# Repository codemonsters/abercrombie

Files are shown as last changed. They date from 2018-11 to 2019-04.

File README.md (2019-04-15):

# Abercrombie

Four-legged educational and minimalist robot using an Arduino Nano board, two SG90 servos and five easy to print parts.

Its design is extremelly simple and it is meant to be used in the classroom or by anyone who wants to build his first robot from scratch.

([versión en español aquí](README.es.md))

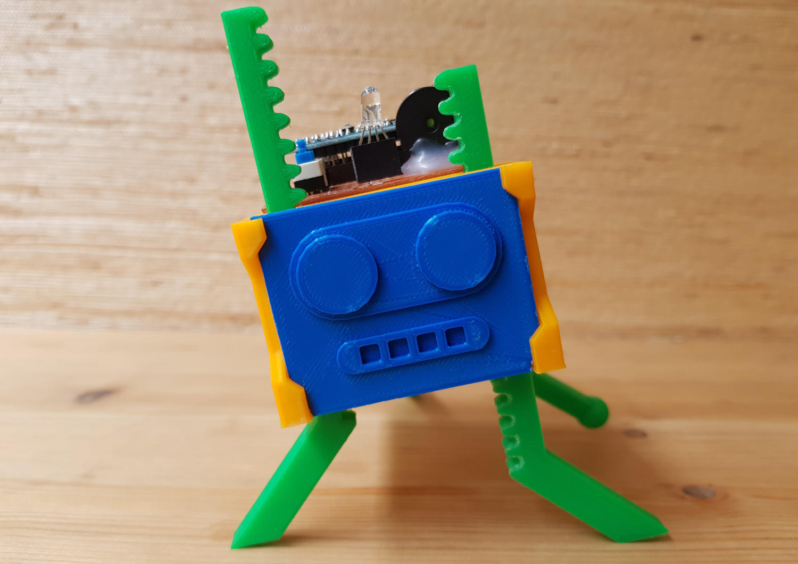
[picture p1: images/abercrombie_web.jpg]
Abercrombie


## Motivation

The general design and also the mechanism that allows the robot to move around is based in an awesome project by Randy Sarafan [published here](https://www.instructables.com/id/3D-Printed-Robot/). After reaching the project for the first time and building one it seemed that a four-legged minimalist robot like his is a great idea. For didactic purposes it would be great to have a similar one but just smaller, easier to print and build with components even cheaper and easier to find in any place you live.

So the robot was designed to be built, customized and programmed in the classroom. It wants to be a starting point so kids, teenagers and of course anyone else interested can created his first walking robot. Its design is intentionally simplistic, trying to be friendly even for people not initiated in programming, electronics or 3D printing.

The robot can be used in educational activities dedicated to different aspects of robotics:

* Work only in the design and 3D printing customizing the robot with our own designs, assembling it with just a scissor and a screwdriver.
* Turn the activity more into electronics making use of perfboards, soldering irons and including different electronic components.
* Use the robot for programming activities: defining the instructions that form every movement or creating programs that control any sensor or actuator we have attached to the robot.
* Treat all the pointed challenges together.

## General characteristics

Pros:

* Simple and completely open design with a very permissive license (GPL3 for the code and CC BY-NC-SA 4.0 for the 3D printed parts).
* Standard and extremelly simple electronics: mostly just two SG90 servos, one Arduino Nano board, a Nano sensor shield (or a perfboard) and a 9V battery.
* Very easy to print: just a few parts of reduced size that don't need support material while printing.
* Customizable: Creating new designs for any of his parts, but also because the chassis has connectors in the front area to attach any new piece designed by us.
* Extensible: After soldering an Arduino Nano board the perfboard should have enough free space to add extra components: a buzzer, LED lights, an ultrasonic sensor, LDR resistors...
* It is a four-legged robot. And a bit clumsy, but it is also friendly looking and funny while walking.

Cons:

* It is a four-legged robot. Sure this is also and disadvantage and his movement is not suited for certain activities where robots with wheels are much better (i.e.: using it with line following circuits).

## Friendly for the classroom

The robot can be used and also built in the classroom: it is simple, price per unit is very low and printing times for all the parts are quiet reasonable. Denpeding on the size of the group and the number of printers available it could be feasible to build one per student.

The design of the robot is suited to focus the activity in any of the main areas of robotics:
* Mechanics: It uses a gear, two gear racks and servomotors.
* Electronics: It is possible to build the robot soldering the needed components in a standard perfboard and add new elements. On the other hand is also possible to simplify its construction using an Arduino Nano sensor shield. That way one should just plug the connectors to the board using his bare hands.
* Programming: Even with its simplistic design, the robot can be programmed to walk forward, backwards and to turn in both directions.

The chassis of the robot has four connectors in the front to allow attaching swappable parts. These part could have aesthetic purposes (a new face for the robot) or even functional.

## Current state of the project

The current design of the robot is ready to be built with both kind of boards (sensor shield or perfboard) and it is also able to make all the basic movements it was meant for (walking forward, backward and turning in both directions).

## Version history

* v1.4: Design improvements in the chassis to allow attaching both a perfboard or a Nano sensor shield.
* v1.3: Small modifications in the chassis to minimize completely horizontal hanging areas.
* v1.2: Chassis design changed to be printed in less time and using less material.
* v1.1: Several parts modified to be printed without support material.
* v1.0: First working version.

## Gallery

Screenshots (pictures captured with the phone... sorry) showing the design of the parts:

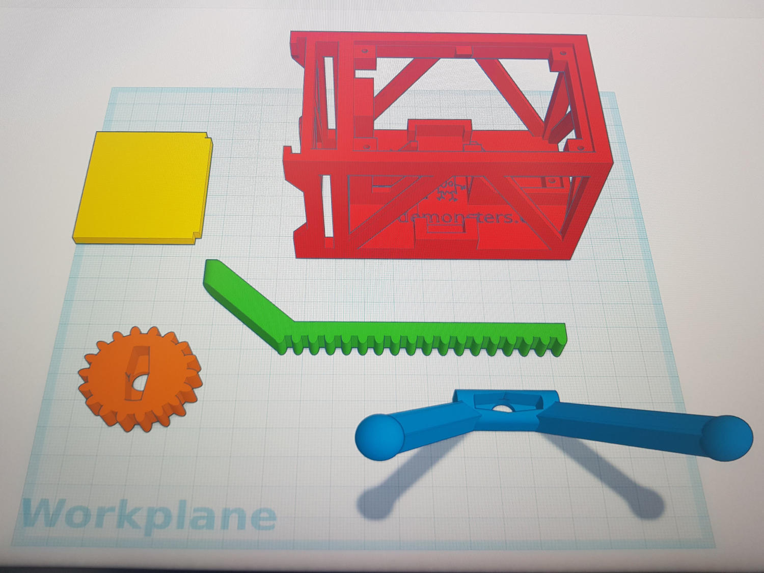
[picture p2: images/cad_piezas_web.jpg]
CAD parts


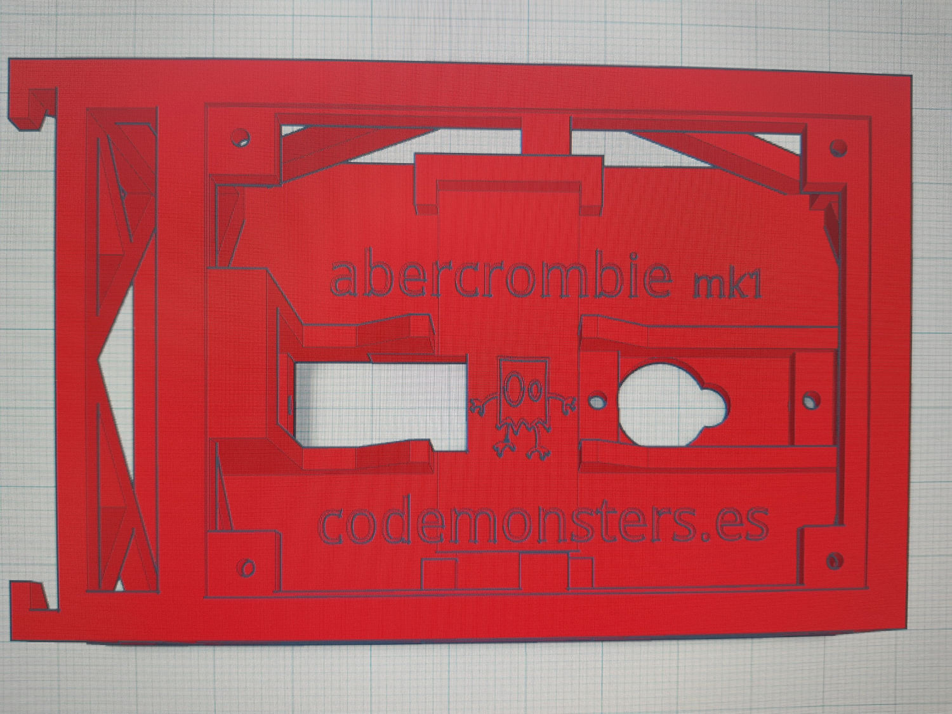
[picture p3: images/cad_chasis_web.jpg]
CAD chassis


Chassis just printed (no support material used):

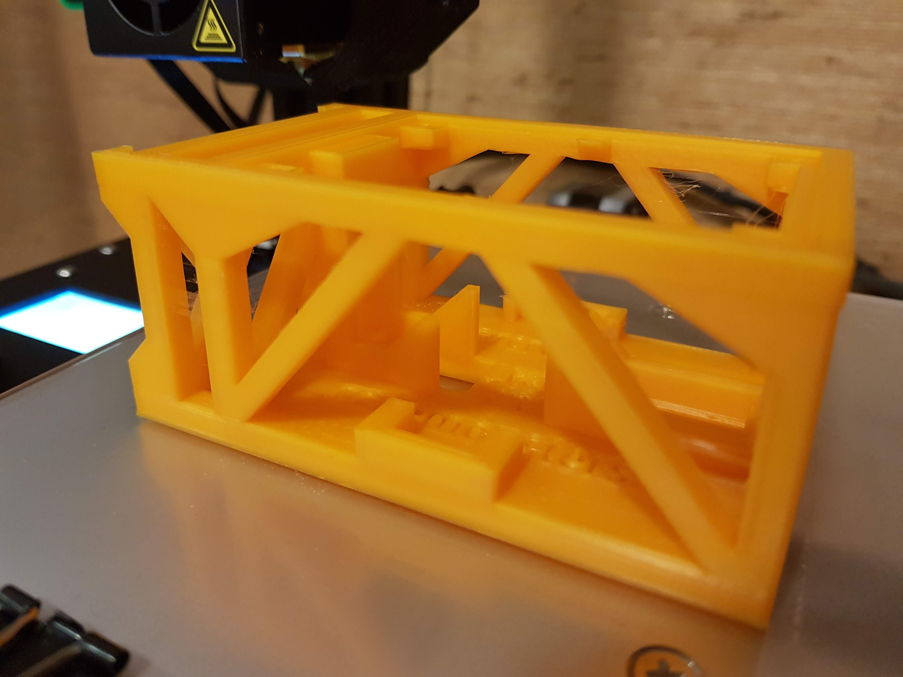
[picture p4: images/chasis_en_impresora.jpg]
Chassis in printer


Several sets of parts ready to be used in an activity:

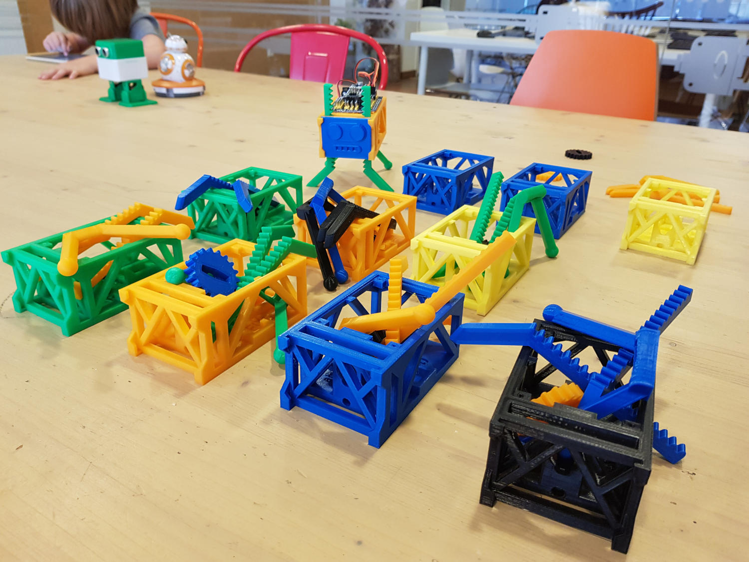
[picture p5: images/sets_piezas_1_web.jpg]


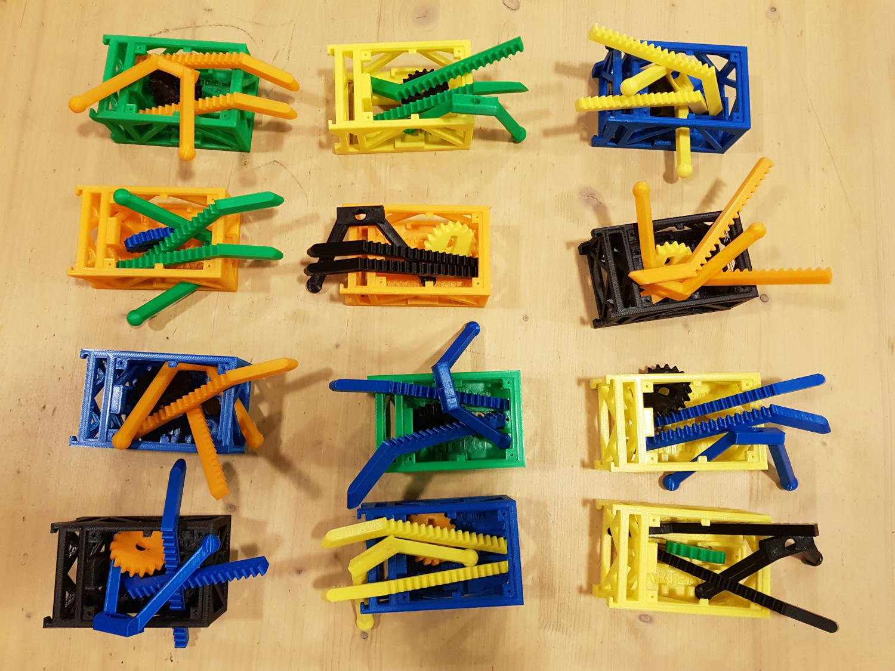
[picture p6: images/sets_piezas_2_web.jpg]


Video with his first steps (prototype):

Video with his first steps (prototype) (https://www.youtube.com/watch?v=WuDx59RuUR0)

They are alive! Robots built and customized during an activity:

¡Están vivos! (https://www.youtube.com/watch?v=RpZjiBUb5sI)

Perfboard with an Arduino Nano soldered but also with added temporary switches to program the sequence of movements, a buzzer, a RGB LED and a power switch:

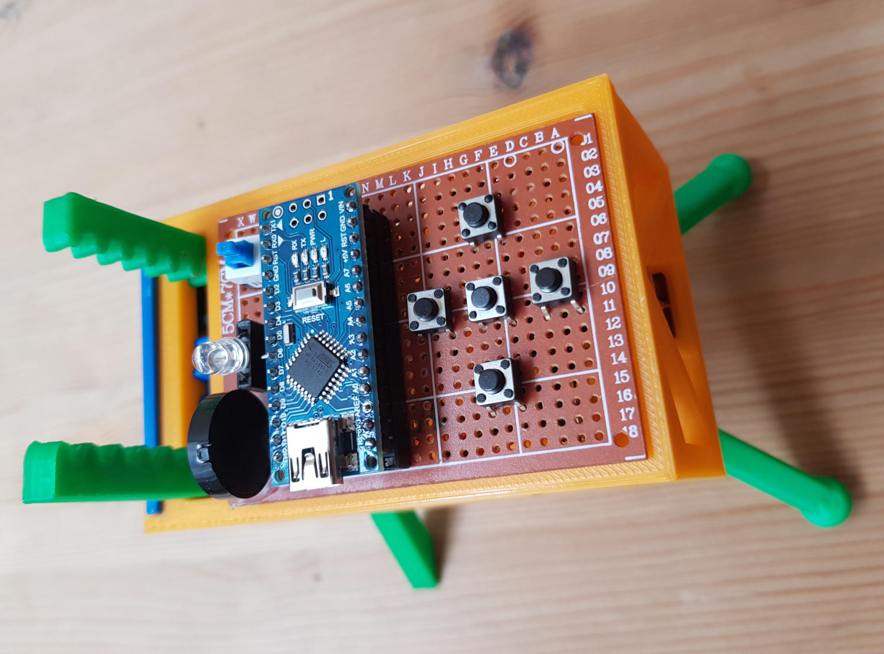
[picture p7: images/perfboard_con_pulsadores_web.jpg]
Perfboard with components


Prototype that uses a sensor shield. Plug & play assembly: zero soldering, the connections between the battery and the board used a standard power jack and the servos are directly connected to the sensor board using its own triple DuPont female connector, no modifications needed).

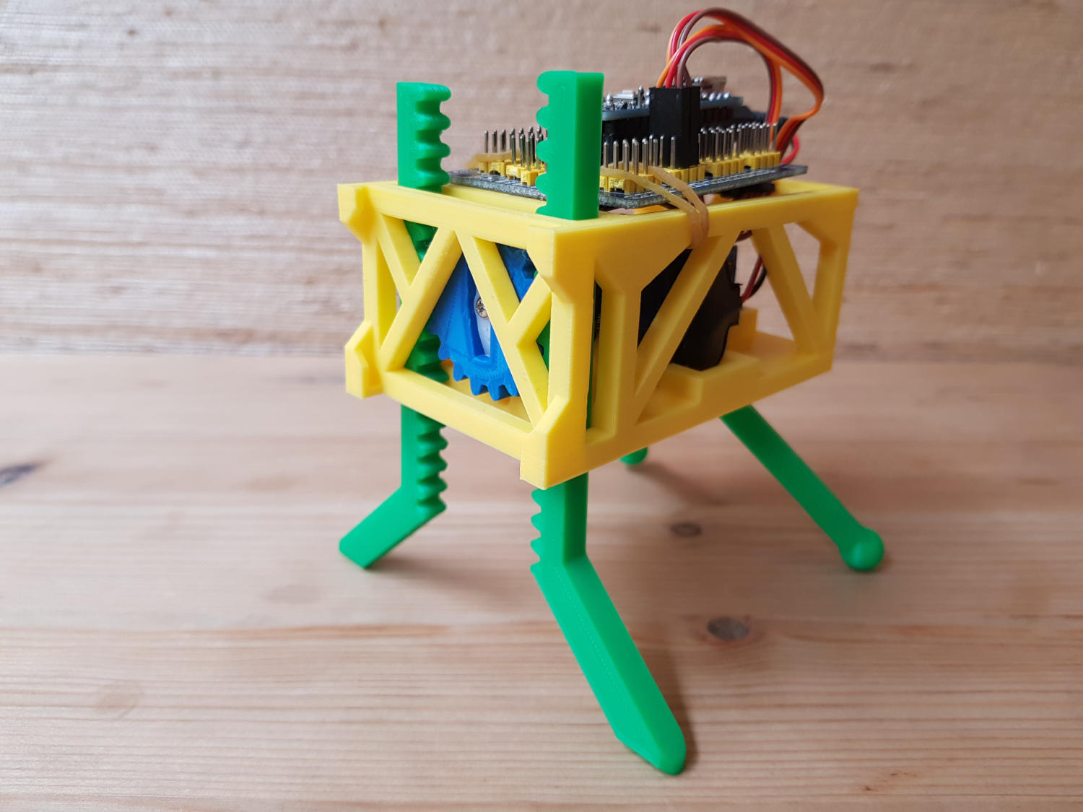
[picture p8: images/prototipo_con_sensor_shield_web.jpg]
Prototype using a sensor shield


## Bill of materials

* 1x Arduino Nano board
* 2x SG90 servos
* In case you want to solder everything:
    * 1x perfboard
    * 1x Arduino Nano socket
    * 1x power switch (breadboard friendly)
    * 1x LR6 9v battery connector
    * Any other component you want to add: a buzzer, LEDs, LDR resistors...
* If you choose to simplify things and avoid soldering:
    * 1x Arduino Nano Sensor Shield
    * 1x LR6 9v battery connector with an Arduino compatible jack
* 1x LR6 9v battery
* And print these parts (the models are published in the [stl](./stl) folder):
    * 1x chassis
    * 1x gear
    * 1x rear legs
    * 2x forward legs

## Construction

In case you are using the Nano sensor shield the connections are just a matter of pluging the rear and the forward data cables of the servos (usually the orange ones) to any two PWM enabled pins you want. Just remember to define the same pin numbers later in the sketch when you are programming the robot. Both red cables of the servos should be connected to a 5v output pin of the board and the brown ones to ground (GND).

If you prefer to use a perfbord you can use this basic electrical diagram as reference:

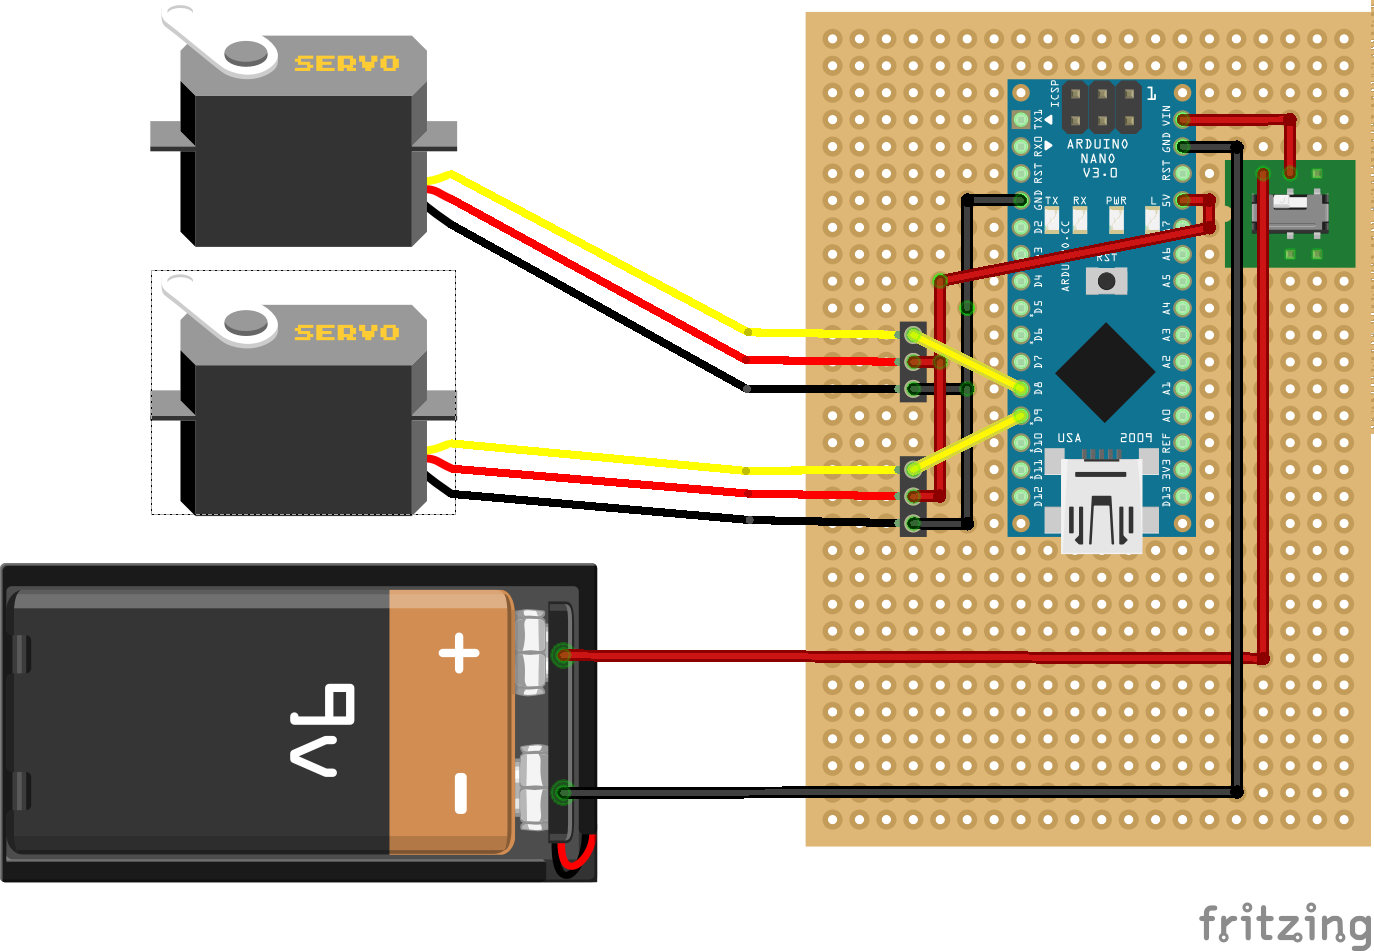
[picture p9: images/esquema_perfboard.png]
Electrical diagram


Former diagram shows a simple robot, with connections between the two servos and the board and an added power switch. Place the Arduino Nano board so it has the USB connector to the right if you want to have more free space to add extra components like switches to program sequences of movements, a buzzer to make sounds, an RGB LED or any other component.

Once you have the printed parts and the rest of the material ready, most of the assembly procedure should be self-explanatory. Anyway some details should be noted:

* Start cutting with a pair of scissors or an x-acto knife the plastic headers that come with the servo so that one of them fits inside the gear and the other inside the rear legs.
* Make sure that both servos are in their center position before assembling them (the same plastic headers can be used to turn them manually until they are centered).
* Maybe you need to polish the upper part of the hole where the front servo needs to be attached. Anyway you will need to apply a bit of force to insert the servos because the design of this areas is deliberately tight (so you won't need extra screws for the servos in most of the cases).
* When assembling the frontal mechanism all the printed parts will have to be inserted simultaneously (two front legs and the gear). Take in count that everything should be in the central position and so after placing all the frontal parts you should have more or less the same number of teeth over the axis of the motor than under itself. After finishing placing the parts tight the screw of the frontal servo and optionally secure the servo with two more screws.
* Rear feet have an spherical design to optionally add "sockets" to improve the grip while walking (i.e: two small water balloons or any other material).

## Arduino Sketches

In [src](./src) folder there are two example Arduino sketches:

* minimum.ino: Basic forward movement. Didactic code with maximum simplification.
* abercrombie.ino: It has functions to move forward, backward and turn in both directions. It also has added definitions to easily adjust how the robot works based on the center position of each servo (to correct by software the small calibration errors that could happen while trying to find the center position of each servo.

## Collaborate

If you build your own robot or you use it in any educational activity please send a picture. It would be great seeing it!

Did you make any improvement or modification? Share your work so we all can make this project better!

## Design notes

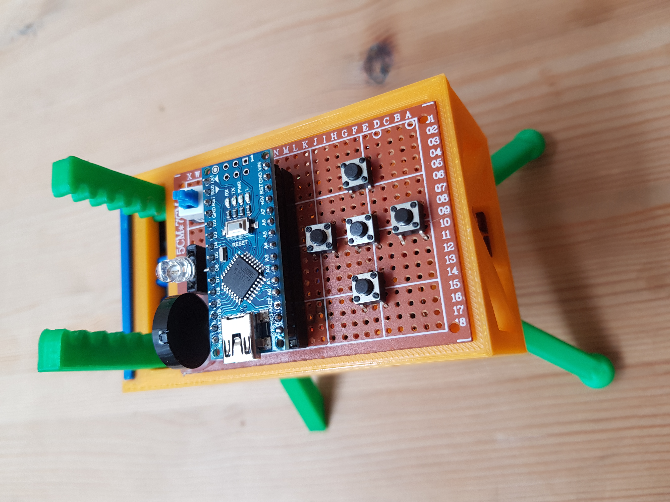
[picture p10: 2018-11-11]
images/perfboard_con_pulsadores.jpg

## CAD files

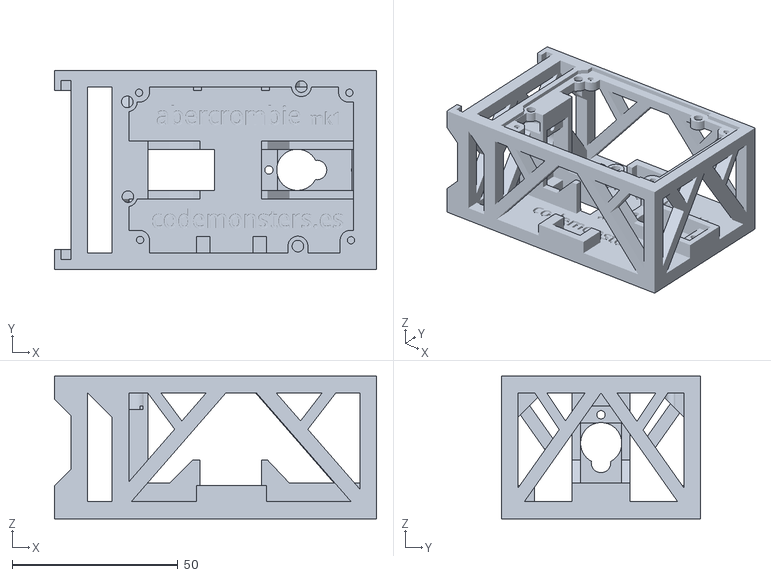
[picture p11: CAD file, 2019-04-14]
stl/chassis v1.4.stl
97.1 x 60.0 x 43.0

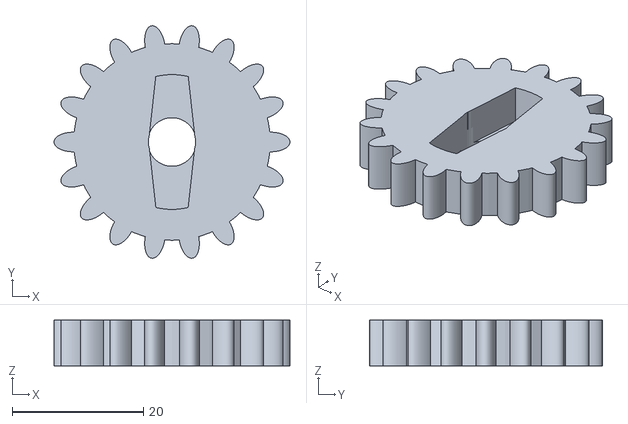
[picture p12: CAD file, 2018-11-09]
stl/gear.stl
36.0 x 35.5 x 7.00

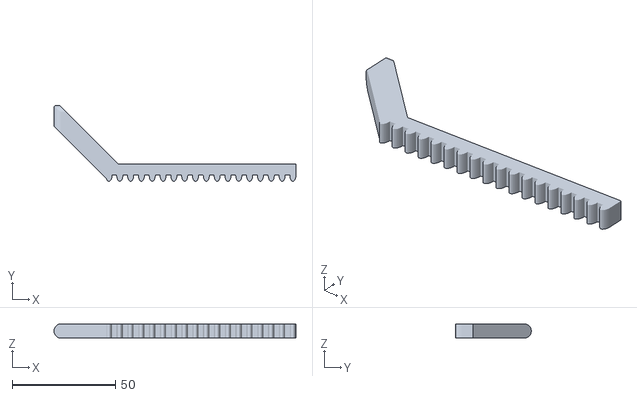
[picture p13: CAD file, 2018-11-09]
stl/front leg.stl
117.1 x 36.6 x 7.00

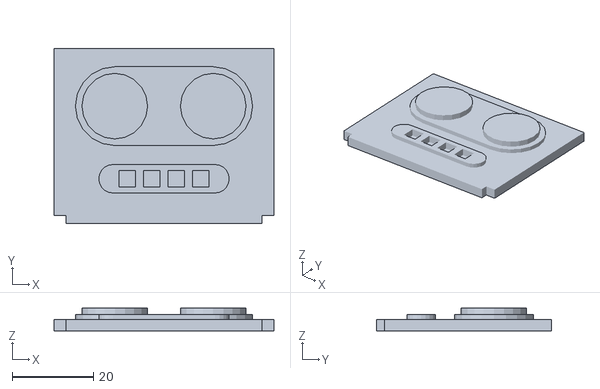
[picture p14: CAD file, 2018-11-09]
stl/sample head.stl
54.0 x 43.0 x 5.60

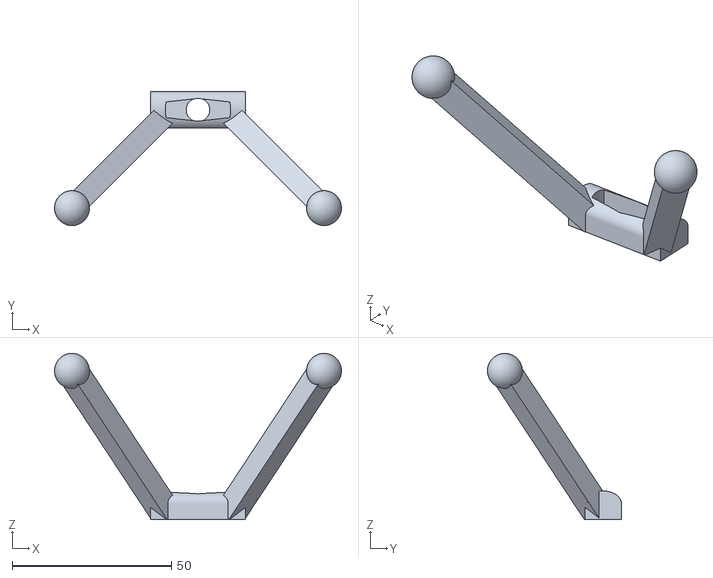
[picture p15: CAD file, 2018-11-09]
stl/rear legs.stl
90.2 x 42.2 x 52.2

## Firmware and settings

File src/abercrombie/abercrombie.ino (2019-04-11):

/*
    Abercrombie
    Four-legged didactic and minimalistic robot / Robot cuadrúpedo didáctico y minimalista
    www.codemonsters.es
*/

#include <Servo.h>

#define FORWARD_SERVO_PIN 8 // pin used to control forward servo
#define REAR_SERVO_PIN 9  // pin used to control rear servo
#define FORWARD_SERVO_CENTER 70  // center position of the forward servo, from 0 to 180
#define REAR_SERVO_CENTER 80     // center position of the rear servo, from 0 to 180
#define FORWARD_MOVEMENT_FACTOR 0.5  // a value between 0 and 1 (make it low to reduce the travel of the forward legs while moving)
#define REAR_MOVEMENT_FACTOR 0.5    // a value between 0 and 1  (make it low to reduce the travel of the rear legs while moving)
#define DELAY_BETWEEN_SERVO_MOVEMENTS 250 // miliseconds to wait between servo movements

Servo forwardServo, rearServo;
int forwardServoMaxRotation = 0;
int rearServoMaxRotation = 0;

void setup()
{
  // Estimate the maximum degrees of movement we have in each servo taking in count the center position defined above (the biggest the defined center is from 90 degrees, the less free degreess we will have)
  if (FORWARD_SERVO_CENTER > 90) {
    forwardServoMaxRotation = 180 - FORWARD_SERVO_CENTER;
  } else {
    forwardServoMaxRotation = FORWARD_SERVO_CENTER;
  }
  if (REAR_SERVO_CENTER > 90) {
    rearServoMaxRotation = 180 - REAR_SERVO_CENTER;
  } else {
    rearServoMaxRotation = REAR_SERVO_CENTER;
  }
  
  // initialize the servos
  forwardServo.attach(FORWARD_SERVO_PIN);
  rearServo.attach(REAR_SERVO_PIN);

  // move both servos to the center position
  standingPosition();

  delay(1000);
}


void loop()
{
  // Add the movements you want your robot to follow
  walkForward();
  //turnLeft();
  //turnRight();
  //walkBackwards();
}

// Walk one step forward
void walkForward(){
    forwardServo.write(FORWARD_SERVO_CENTER + forwardServoMaxRotation * FORWARD_MOVEMENT_FACTOR);
    delay(DELAY_BETWEEN_SERVO_MOVEMENTS);
    rearServo.write(REAR_SERVO_CENTER - rearServoMaxRotation * REAR_MOVEMENT_FACTOR);
    delay(DELAY_BETWEEN_SERVO_MOVEMENTS);
    forwardServo.write(FORWARD_SERVO_CENTER - forwardServoMaxRotation * FORWARD_MOVEMENT_FACTOR);
    delay(DELAY_BETWEEN_SERVO_MOVEMENTS);
    rearServo.write(REAR_SERVO_CENTER + rearServoMaxRotation * REAR_MOVEMENT_FACTOR);
    delay(DELAY_BETWEEN_SERVO_MOVEMENTS);
}

// Turn one step left
void turnLeft() {
  forwardServo.write(FORWARD_SERVO_CENTER);
  rearServo.write(REAR_SERVO_CENTER - rearServoMaxRotation * REAR_MOVEMENT_FACTOR);
  delay(DELAY_BETWEEN_SERVO_MOVEMENTS);
  forwardServo.write(FORWARD_SERVO_CENTER - forwardServoMaxRotation * FORWARD_MOVEMENT_FACTOR);
  delay(DELAY_BETWEEN_SERVO_MOVEMENTS);
  rearServo.write(REAR_SERVO_CENTER + rearServoMaxRotation * REAR_MOVEMENT_FACTOR);
  delay(DELAY_BETWEEN_SERVO_MOVEMENTS);
}

// Turn one step right
void turnRight() {
  forwardServo.write(FORWARD_SERVO_CENTER);
  rearServo.write(REAR_SERVO_CENTER + rearServoMaxRotation * REAR_MOVEMENT_FACTOR);
  delay(DELAY_BETWEEN_SERVO_MOVEMENTS);
  forwardServo.write(FORWARD_SERVO_CENTER + forwardServoMaxRotation * FORWARD_MOVEMENT_FACTOR);
  delay(DELAY_BETWEEN_SERVO_MOVEMENTS);
  rearServo.write(REAR_SERVO_CENTER - rearServoMaxRotation * REAR_MOVEMENT_FACTOR);
  delay(DELAY_BETWEEN_SERVO_MOVEMENTS);
}

// Walk one step back
void walkBackwards() {
  forwardServo.write(FORWARD_SERVO_CENTER);
  rearServo.write(REAR_SERVO_CENTER + rearServoMaxRotation * REAR_MOVEMENT_FACTOR);
  delay(DELAY_BETWEEN_SERVO_MOVEMENTS);
  forwardServo.write(FORWARD_SERVO_CENTER - forwardServoMaxRotation * FORWARD_MOVEMENT_FACTOR);
  delay(DELAY_BETWEEN_SERVO_MOVEMENTS);
  rearServo.write(REAR_SERVO_CENTER - rearServoMaxRotation * REAR_MOVEMENT_FACTOR);
  delay(DELAY_BETWEEN_SERVO_MOVEMENTS);
  
}

void standingPosition() {
  forwardServo.write(FORWARD_SERVO_CENTER);
  rearServo.write(REAR_SERVO_CENTER);
}

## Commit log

2018-11-09 Añadidos archivos STL
    [Cabeza simple.stl, Chasis v1.3.stl, Pata delantera.stl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]
2018-11-10 Añadida lista de materiales
2018-11-10 Añadido sketch Arduino
2018-11-10 Creados nuevos sketches de ejemplo
2018-11-11 Instrucciones de montaje e imágenes añadidas
2019-04-11 Cambios menores en la documentación
2019-04-14 STL file and documentation updated
    [Chasis v1.3.stl, Chasis v1.4.stl]
2019-04-15 STL files renamed
    [chassis v1.4.stl, front leg.stl, gear.stl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]
